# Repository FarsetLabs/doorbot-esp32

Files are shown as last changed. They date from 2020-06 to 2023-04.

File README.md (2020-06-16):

# doorbot-esp32

RFID Card Reader and Door Relay Opening Module for use with the [doorbot](https://www.github.com/FarsetLabs/doorbot) project.

It's general operation is:

* Setup Wi-Fi Connection*
* Setup MFRC522 Card Connection
* Loop waiting for card presence detection
* On Card Detect, Grab the UID from the presented Card
* Attempt to trigger an 'open' action* on the door identified by the onboard device_id, using the same device id and the UID from the presented card as the Username and Password for HTTP Basic Auth
* If 200 response; flash green on RGB LED and unlock door via relay for 5 seconds
* Otherwise flash red for 5 seconds and resume loop

*Configured through build-time environment variables, see `platform.ini` for details

## Hardware Setup

This project uses an ESP-WROOM-32 package, an RC522 RFID module

ESP32 Pinout

RC522 Pinout

### Pin Mappings:

#### RC522 -> ESP32

| RC522 | ESP32 | Description |
| ----- | --- | --- |
| 3v3 | 3v3 | VIN |
| RST | D22 | Reset |
| GND | GND | Ground |
| IRQ | <Blank> | Unused |
| MISO  | D19 | SPI Master Input  |
| MOSI  | D23 | SPI Master Output |
| SCK | D18 | SPI Clock |
| SDA | D21 | Serial Data Line  |

#### RGB LED -> ESP32

| RGB LED | ESP32 | Description |
| --- | --- | --- |
| (-) | GND | Ground |
| R | D2 | Red |
| G | D4 | Green |
| B | <blank> | Blue |

#### RELAY -> ESP32

| RELAY | ESP32 | |
| ----- | ----- | --- |
| NO | D15 | Normally Open (Actuator) |
| + | 3v3 | +VE |
| - | GND | Ground |

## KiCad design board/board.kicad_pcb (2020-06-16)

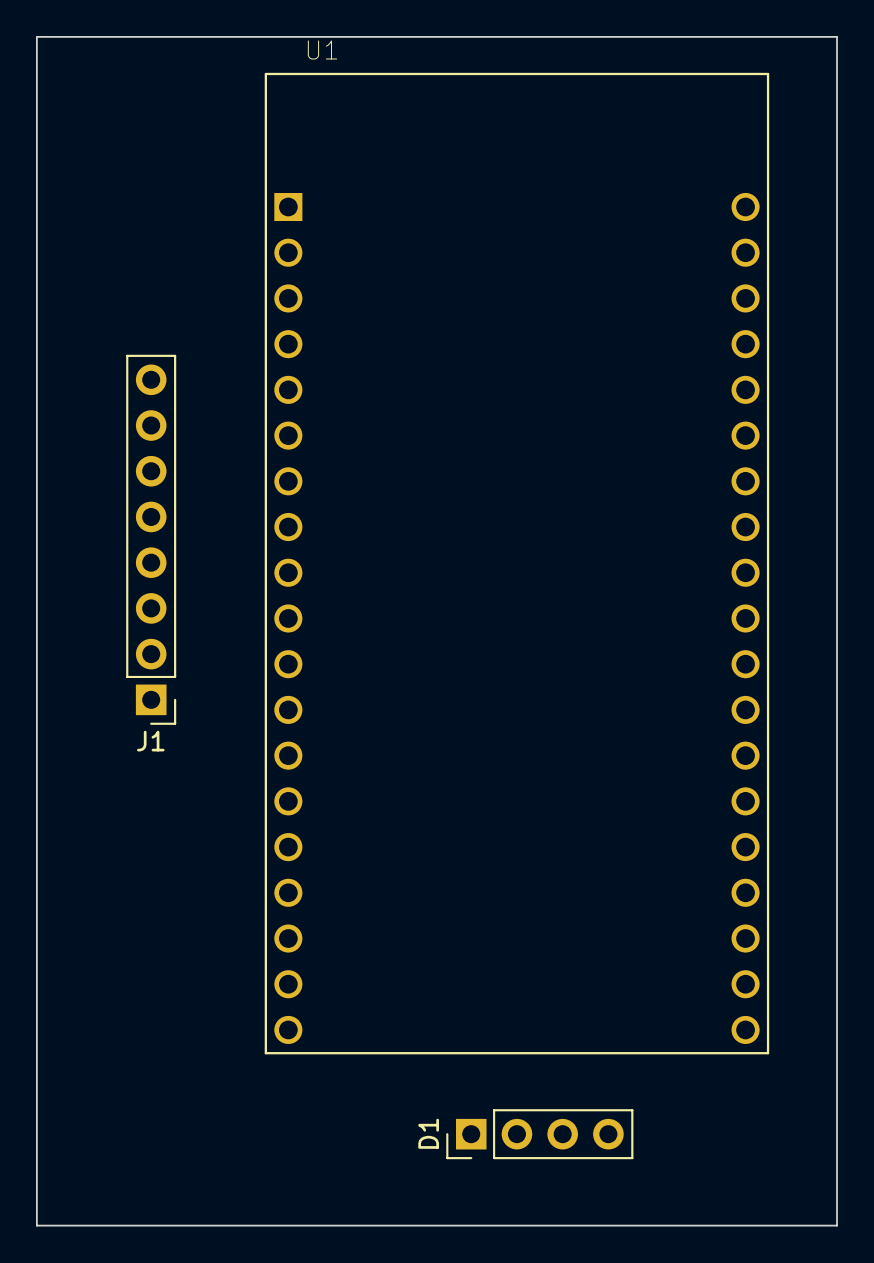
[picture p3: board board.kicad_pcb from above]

Board: 2 copper layers, 44.4 x 66.0 mm, 3 parts (0 on the bottom side), 10 nets, no tracks yet.

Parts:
D1: LED_ARBG; PinHeader_1x04_P2.54mm_Vertical
J1: RFID-RC522; PinHeader_1x08_P2.54mm_Vertical
U1: ESP32-DEVKITC-32D; MODULE_ESP32-DEVKITC-32D

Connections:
unnamed: D1.1, J1.6, U1.2
unnamed: D1.2, U1.5
unnamed: D1.3, U1.4
unnamed: D1.4, U1.3
unnamed: J1.1, U1.15
unnamed: J1.2, U1.13
unnamed: J1.3, U1.19
unnamed: J1.4, U1.14
unnamed: J1.7, U1.18
unnamed: J1.8, U1.1

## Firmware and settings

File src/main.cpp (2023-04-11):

#include <Arduino.h>
#include <ArduinoJson.h>
#include <PubSubClient.h>
#include <MFRC522.h> //library responsible for communicating with the module RFID-RC522
#include <SPI.h> //library responsible for communicating of SPI bus


#ifdef ESP8266
  #include <ESP8266WiFi.h>          //https://github.com/esp8266/Arduino
  #define CHIP_ID   ((uint32_t)ESP.getChipId())
#else
  #include <WiFi.h>
  #include <WiFiClientSecure.h>
  #define CHIP_ID   ((uint32_t)ESP.getEfuseMac())
#endif

#include <WiFiMulti.h>
#include <WiFiClient.h>
#include <HTTPClient.h>

#define SS_PIN    21
#define RST_PIN   22
#define SIZE_BUFFER     18
#define MAX_SIZE_BLOCK  16
#define greenPin     2
#define redPin       4
#define relayPin     15

//used in authentication
MFRC522::MIFARE_Key key;
//authentication return status code
MFRC522::StatusCode status;
// Defined pins to module RC522
MFRC522 mfrc522(SS_PIN, RST_PIN); 

char addr_str[21];  // Stores the scanned ID as a str-able


const int WIFI_CONNECT_TIMEOUT_SECONDS = 10;

WiFiClientSecure wifi_client;
PubSubClient mqtt_client(wifi_client);
HTTPClient http;

String device_id;
String client_id;
String pub_topic;
String sub_topic;
String space_name = SPACE_NAME;

struct HTTPResponse {
   int status_code;
   String response;
};

String get_device_id() {
  uint64_t mac_integer = CHIP_ID;
  uint8_t *mac = (uint8_t*) &mac_integer;
  char mac_chars[13];
  for (int i=0; i<6; i++) {
    sprintf(mac_chars + i * 2, "%" PRIx8, mac[i]);
  }
  return mac_chars;
}

boolean connect_wifi() {
  Serial.print(F("Connecting to wifi "));
  Serial.println(WIFI_SSID);
  WiFi.disconnect() ;
  WiFi.mode(WIFI_STA);
  WiFi.begin(WIFI_SSID, WIFI_PASS);
  for (int i=0; i<WIFI_CONNECT_TIMEOUT_SECONDS && WiFi.status() != WL_CONNECTED; i++) {
    delay(1000);
    Serial.print(".");
  }
  Serial.println("");
  if (WiFi.status() == WL_CONNECTED) {
    Serial.print(F("Connected to "));
    Serial.println(WIFI_SSID);
    Serial.print(F("IP address: "));
    Serial.println(WiFi.localIP());
    return true;
  } else {
    Serial.println(F("Failed to connect to WiFi; current status = "));
    Serial.println(WiFi.status());
    return false;
  }
}

void mqtt_callback(char* topic, byte* payload, unsigned int length) {
 
  Serial.print("Message arrived in topic: ");
  Serial.println(topic);
 
  Serial.print("Message:");
  for (int i = 0; i < length; i++) {
    Serial.print((char)payload[i]);
  }
 
  Serial.println();
  Serial.println("-----------------------");

  StaticJsonDocument<256> doc;
  deserializeJson(doc, payload, length);
  JsonObject object = doc.as<JsonObject>();
  String new_state = object["state"];
  Serial.println(new_state);
  
}

boolean reconnect_mqtt() {
  if (mqtt_client.connected()) {
    Serial.println(F("Still connected to MQTT broker"));
  }
  Serial.println(F("Reconnecting to MQTT broker"));
  mqtt_client.connect(client_id.c_str());
  if (mqtt_client.connected()) {
    Serial.println(F("Connected to MQTT broker"));
    mqtt_client.subscribe(sub_topic.c_str());
    return true;
  } else {
    Serial.println(F("Failed to connect to MQTT broker"));
    Serial.print(mqtt_client.state());
    Serial.println(" try again in 5 seconds");
    // Wait 5 seconds before retrying
    delay(5000);
    return false;
  }
}

void array_to_string(byte array[], unsigned int len, char buffer[])
{
    for (unsigned int i = 0; i < len; i++)
    {
        byte nib1 = (array[i] >> 4) & 0x0F;
        byte nib2 = (array[i] >> 0) & 0x0F;
        buffer[i*2+0] = nib1  < 0xA ? '0' + nib1  : 'A' + nib1  - 0xA;
        buffer[i*2+1] = nib2  < 0xA ? '0' + nib2  : 'A' + nib2  - 0xA;
    }
    buffer[len*2] = '\0';
}

//reads data from card/tag
boolean readCardId()
{
  //prints the technical details of the card/tag
  mfrc522.PICC_DumpDetailsToSerial(&(mfrc522.uid)); 
  
  //prepare the key - all keys are set to FFFFFFFFFFFFh
  for (byte i = 0; i < 6; i++) key.keyByte[i] = 0xFF;
  
  //buffer for read data
  byte buffer[SIZE_BUFFER] = {0};
 
  //the block to operate
  byte block = 1;
  byte size = SIZE_BUFFER;  //authenticates the block to operate
  status = mfrc522.PCD_Authenticate(MFRC522::PICC_CMD_MF_AUTH_KEY_A, block, &key, &(mfrc522.uid)); //line 834 of MFRC522.cpp file
  if (status != MFRC522::STATUS_OK) {
    Serial.print(F("Authentication failed: "));
    Serial.println(mfrc522.GetStatusCodeName(status));
    digitalWrite(redPin, HIGH);
    delay(1000);
    digitalWrite(redPin, LOW);
    return false;
  }

  //read data from block
  status = mfrc522.MIFARE_Read(block, buffer, &size);
  if (status != MFRC522::STATUS_OK) {
    Serial.print(F("Reading failed: "));
    Serial.println(mfrc522.GetStatusCodeName(status));
    digitalWrite(redPin, HIGH);
    delay(1000);
    digitalWrite(redPin, LOW);
    return false;
  }
  else{
    digitalWrite(greenPin, HIGH);
    delay(100);
    digitalWrite(greenPin, LOW);
  }

  array_to_string(mfrc522.uid.uidByte, mfrc522.uid.size, addr_str);
  Serial.println(addr_str);

  return true;
}

void setup() 
{
  Serial.begin(115200);
  SPI.begin(18, 19, 23, 21); //SCK, MISO, MOSI, SS // Init SPI bus
  //Heltec.begin(true /*DisplayEnable Enable*/, false /*LoRa Enable*/, true /*Serial Enable*/);

  pinMode(greenPin, OUTPUT);
  pinMode(redPin, OUTPUT);
  pinMode(relayPin, OUTPUT);

  digitalWrite(greenPin, LOW);
  digitalWrite(redPin, HIGH);
  digitalWrite(relayPin, HIGH);

  while(!connect_wifi()){
    Serial.println("Couldn't connect to Wifi, sleeping for 5 seconds");
    ESP.deepSleep(5*1e6);
  }
  Serial.print("Connected; Device ID: ");
  Serial.println(get_device_id());

  // Init MFRC522
  mfrc522.PCD_Init(); 
  digitalWrite(greenPin, LOW);
  digitalWrite(redPin, LOW);
  digitalWrite(relayPin, LOW);
  Serial.println("Approach your reader card...");
  Serial.println();

  wifi_client.setInsecure();
}

HTTPResponse make_request(){
  HTTPResponse response;
  // Lets play nexudus!
  //
  http.begin(wifi_client, "https://"+space_name+".spaces.nexudus.com/api/public/checkin"); 
  http.addHeader("Content-Type", "application/json");
  response.status_code = http.POST(
    "{\"AccessCardID\":\""+String(addr_str)+"\"}"
  );
  Serial.println(addr_str);

  if (response.status_code>0) {
    
    Serial.print("HTTP Response code: ");
    Serial.println(response.status_code);
    response.response = http.getString();
    Serial.println(response.response);
  }
  else {
    Serial.print("Error code: ");
    Serial.println(response.status_code);
    Serial.println(http.getString());
  }
  // Free resources
  http.end();

  return response;
}


void loop() {

   //waiting the card approach
  if ( ! mfrc522.PICC_IsNewCardPresent()) 
  {
    delay(400);
    digitalWrite(greenPin, HIGH);
    delay(100);
    digitalWrite(greenPin, LOW);
    return;
  }
  // Select a card
  if ( ! mfrc522.PICC_ReadCardSerial()) 
  {
    return;
  }

  // Dump debug info about the card; PICC_HaltA() is automatically called
  //  mfrc522.PICC_DumpToSerial(&(mfrc522.uid));</p><p>  //call menu function and retrieve the desired option
  
  if (readCardId()) {
    HTTPResponse response = make_request();
    // Nexudus helpfully doesn't use HTTP status as actual status, so we hae to break the previous doorbot 'cleverness' (thank goodness)
    DynamicJsonDocument doc(1024);
    deserializeJson(doc, response.response);
    if (doc["Status"].as<int>()==200){
      Serial.print("Authorised:");
      Serial.println(doc["Value"]["FullName"].as<String>());
      digitalWrite(greenPin, HIGH);
      digitalWrite(relayPin, HIGH);
      delay(5000);
      digitalWrite(greenPin, LOW);
      digitalWrite(relayPin, LOW);
    } else {
      Serial.println("Unuthorised");
      for (int i = 0; i < 5; i++){
        digitalWrite(redPin, HIGH);
        delay(100);
        digitalWrite(redPin, LOW);
        delay(100);
      }
    }
  }
 
  //instructs the PICC when in the ACTIVE state to go to a "STOP" state
  mfrc522.PICC_HaltA(); 
  // "stop" the encryption of the PCD, it must be called after communication with authentication, otherwise new communications can not be initiated
  mfrc522.PCD_StopCrypto1();  
}
